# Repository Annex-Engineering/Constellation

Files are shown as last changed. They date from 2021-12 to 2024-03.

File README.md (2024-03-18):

# Constellation
Constellation is a series of control boards, powered by the Raspberry Pi Pico board, developed by the team at ANNEX Engineering.

It is intentional that there are no gerbers/schematics/source files available for the forseeable future. This is to prevent clones popping up that use lower quality components.

## Klipper Configurations

Configurations can be found here

## Supernova
 - Supernova, is a 4 stepper controller. 
 - Can drive steppers at 12v to 48v
 - Supports sensorless or switch based endstops
 - Standard Stepstick format supported only
 - Uses XH or Microfit connectors to connect to steppers, such that currents of 3A+ can be supported

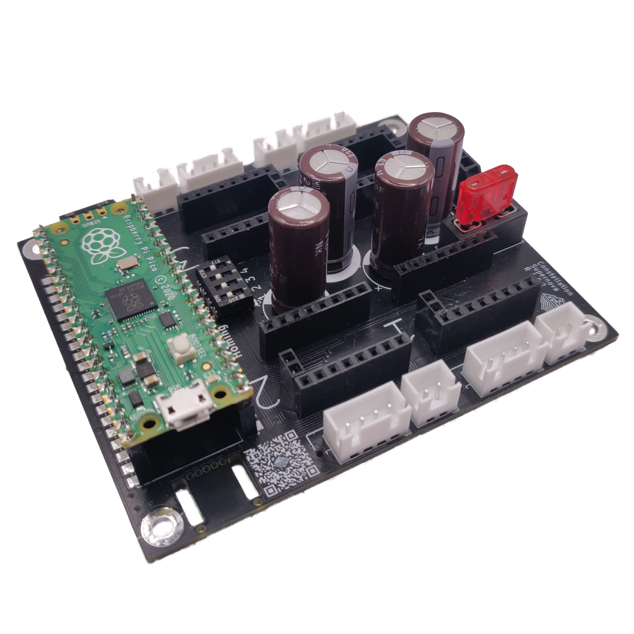
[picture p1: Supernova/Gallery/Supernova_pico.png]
 

 ## Sirius
 TBD

 ## Nebula
 TBD

Our discord server can be found here: 

Join me on Discord (https://discord.gg/MzTR3zE)

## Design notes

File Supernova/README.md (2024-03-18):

# Supernova R1.0.2 - FAQ


Assembled Constellation Supernova R1 with socketed Raspberry Pico.

## Warning
Using 48V electronics can cause serious harm on injury, only attempt to install this on your printer if you know what you are doing.

Under no circumstances we can be held responsible for harm or injury to any person or piece of equipment and you waiver all rights to hold us responsible for anything that happens as a result of using this design, or even thinking about the design.

## Klipper Configurations

Configurations can be found here

## Motor Wiring & Current Limitations

Supernova is rated to handle a total of 8.5 A current combined and up to 48v for all motors. However, most setups will not reach this limit.  
The limit for each individual motor is dependent on the motor itself and the stepper driver used.
When utilizing over 2A on a stepper it's highly recommended to use Microfit instead of JST XH for the stepper wiring.

## Stepper drivers
There are multiple HV-options (beyond 24V), the maximum safe voltage depends on the components the manufacturer puts on the board. This table is an overview for the most used driver chips, the maximum current they can handle (with sufficient cooling) and if they use SPI or UART.  
The following tables are for the step sticks of different manufacturers and which voltage is the maximum safe voltage recommended.  
The tables are using data which has been shamelessly copied from the fine folks at the [powerBrrr-github](https://github.com/tehmaze/PowerBRRR#stepper-drivers). All currents are specified as RMS.

| Driver chip | Max theoretical voltage | Max current | 'SPI' Dipswitch | 
|-|-|-|-|
| TMC2208 |  33V | 2A | Off for UART |
| TMC2209 |  25V | 2.8A | Off for UART |
| TMC2130 |  46V | 1.2A | On for SPI |
| TMC5160 |  **48V** | 3A | On for SPI |

#### BigTreeTech

| Product | Driver chip | Max safe voltage
|-|-|-|
| BigTreeTech TMC2130 | TMC2130 |  42V | 
| BigTreeTech TMC5160 | TMC5160 |  32V | 
| BigTreeTech TMC5160 Pro | TMC5160 |  **48V** | 
| BigTreeTech TMC2208 | TMC2208 |  33V | 
| BigTreeTech TMC2209 | TMC2209 |  25V | 

#### Fysetc
| Product | Driver chip | Max safe voltage
|-|-|-|
| Fysetc TMC2130 | TMC2130 | 42V |
| Fysetc TMC5160| TMC5160 | 32V | 
| Fysetc TMC5160 HV | TMC5160 | **48V** | 
| Fysetc TMC5160 QHV | TMC5160 | **48V** | 
| Fysetc TMC2208 | TMC2208 |  33V | 
| Fysetc TMC2209 | TMC2209 |  25V | 

#### Watterott
| Product | Driver chip | Max safe voltage
|-|-|-|
| Watterott TMC2130 | TMC2130 | 42V | 
| Watterott TMC5160 HV | TMC5160 | **48V** | 
| Watterott TMC2208 | TMC2208 | 33V |
| Watterott TMC2209 | TMC2209 | 25V | 

#### Other
| Product | Driver chip | Max safe voltage
|-|-|-|
| IdeaFormer TMC2130 V1.2 | TMC2130 | 42V |
| Mellow Fly TMC2209 | TMC2209 | 25V |
| Mellow Fly TMC5160 HV | TMC5160 | 42V |
| Mellow Fly TMC5160 HV Pro | TMC5160 | 42V |

## Sensorless Homing
To enable sensorless homing for e.g. Stepper 1 switch the Dipswitch labeled 'Homing' to **On* where '1' is written on the PCB  
Please note, that in the klipper-config most step sticks require diag0 to be set. However the following step sticks are known to require diag1 to be set (instead of diag0)
- Mellow TMC5160 HV
- Watterott TMC5160
- BigTreeTech TMC5160
- BigTreeTech TMC5160 Pro
  
## Dimensions
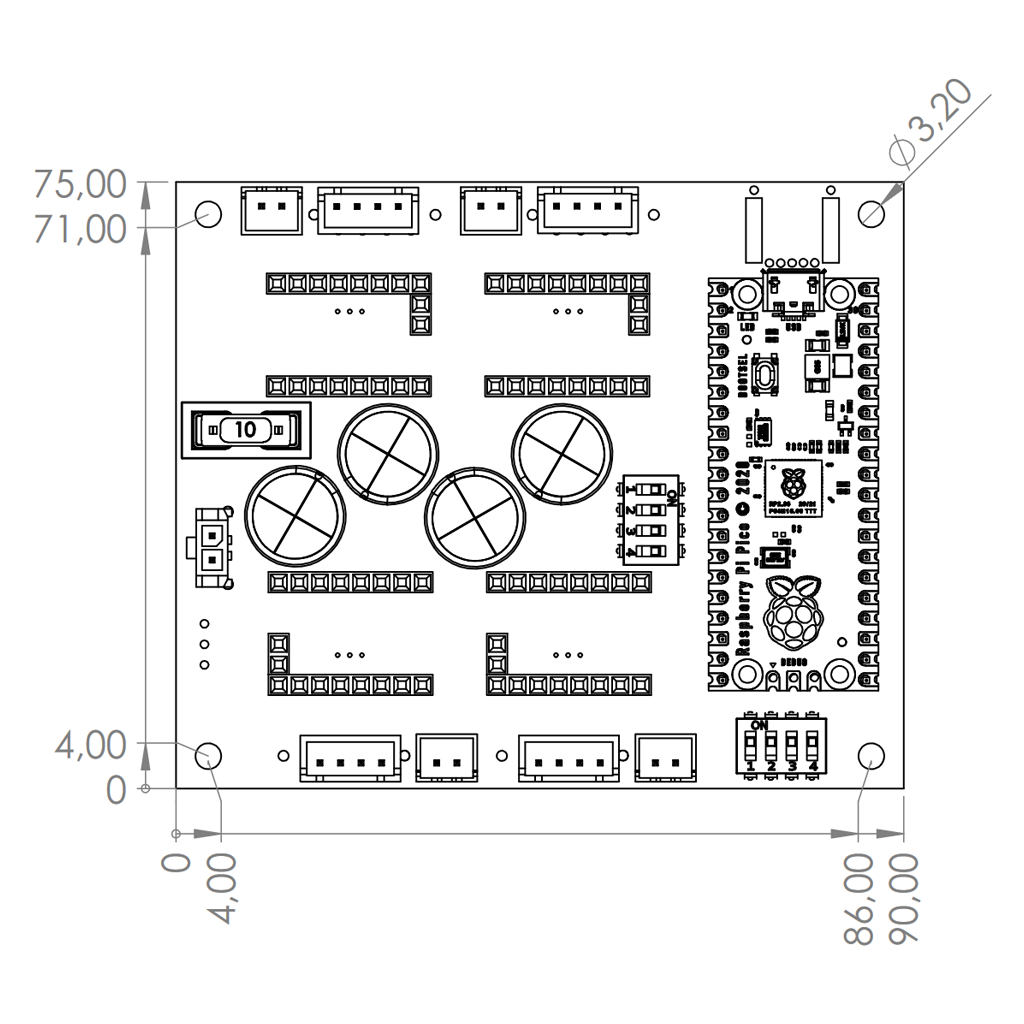
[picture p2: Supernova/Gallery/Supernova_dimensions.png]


The board measures 90x75mm. The mounting holes are spaced apart 82/67mm. 

## Pinout
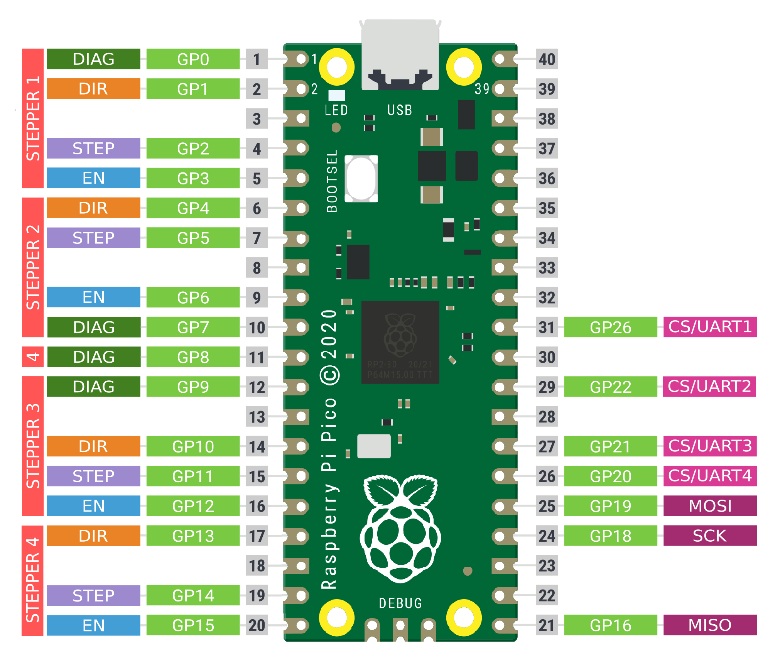
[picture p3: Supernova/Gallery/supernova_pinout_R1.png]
Supernova Pinout


## Flashing Klipper to the Raspberry Pico

> :warning: **If you are using a Raspberry Pi model 4 for Klipper**: Get a good quality USB hub to connect the constellation hardware. The Pi model 4 has a mediocre USB chip that can cause issues in this setup.

To compile the micro-controller code, start by running these commands
on the Raspberry Pi:

```
cd ~/klipper/
make menuconfig
```

Select the Raspberry Pico as controller and review any other options provided. One can enable in the menu to turn on a green LED indicator when powered on. Once configured, run:

```
make
```

Once compiled transfer the .UF2 file to the storage of the Raspberry Pico. This can be done by holding down the button and connecting it to the computer. It will show up as storage device in your file explorer. When done copying to the device it will automatically unmount. The Raspberry Pico is now flashed and ready for use.

Enabling a green LED when powered on can also be done afterwards in the printer.cfg by adding the following:

```
[output_pin power_LED]
pin: gpio25
value: 1
```

## Gallery
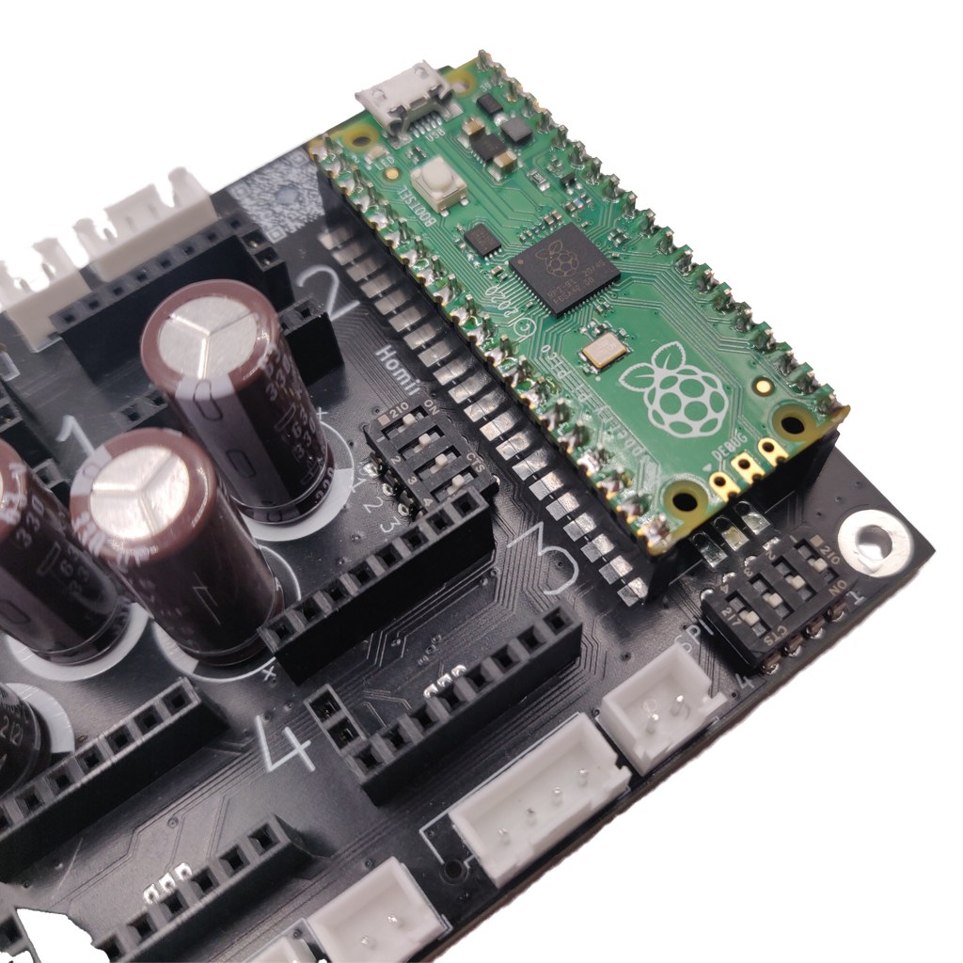
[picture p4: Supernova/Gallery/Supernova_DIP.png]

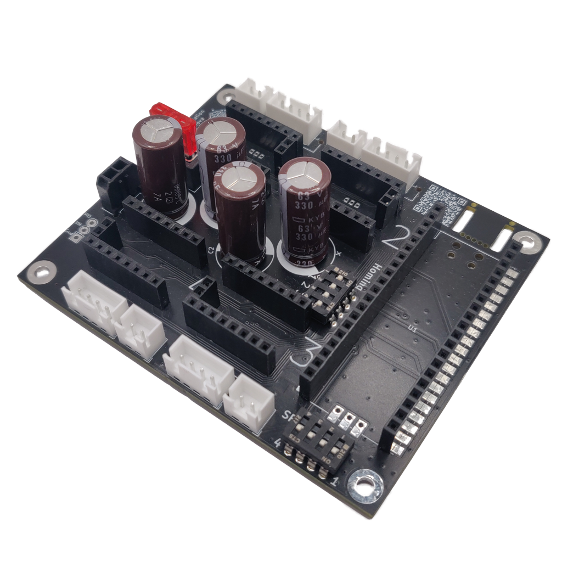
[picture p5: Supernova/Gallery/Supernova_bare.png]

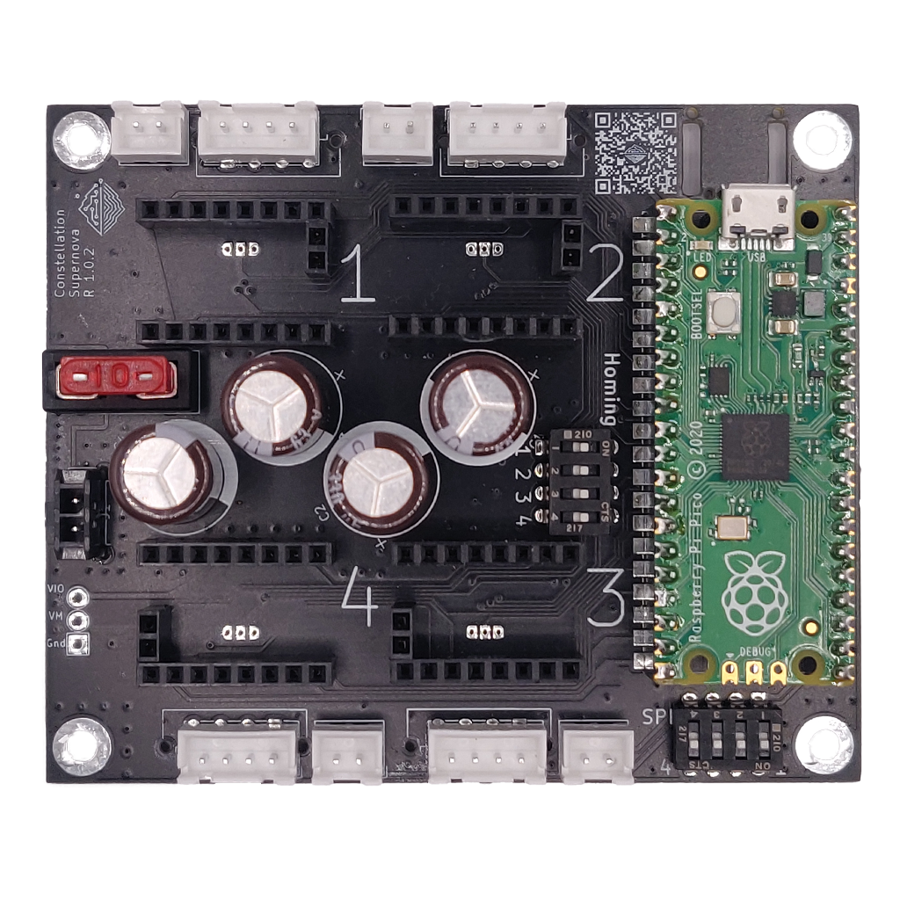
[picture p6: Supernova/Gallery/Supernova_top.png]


## Sourcing
Links to purchase fully assembled boards can be found here: [ANNEX Sourcing Guide](https://docs.google.com/spreadsheets/d/1aSM1jGxg-s0tyynyR3f8M0IQMXuXw57RJvoJbt98Clw/edit?usp=sharing)

Our discord server can be found here: 

Join me on Discord (https://discord.gg/MzTR3zE)

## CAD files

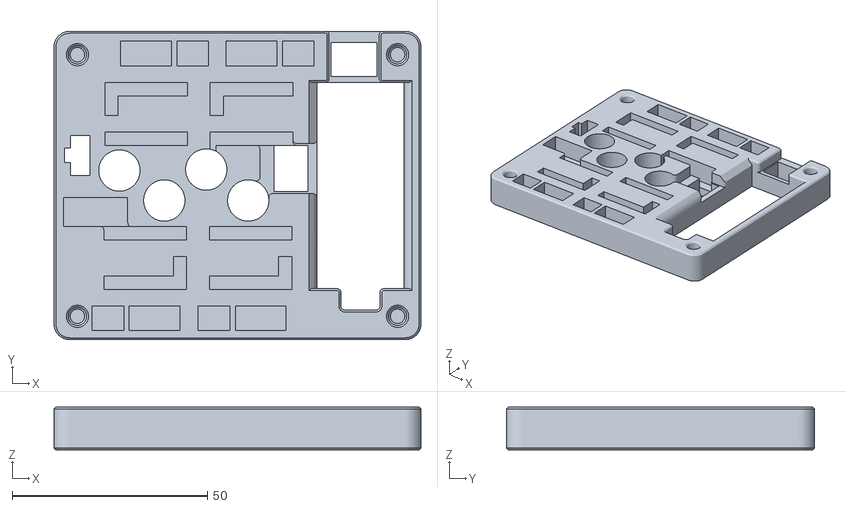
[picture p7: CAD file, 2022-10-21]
Supernova/Assembly_Jig/supernova_assembly_jig_10-21-22_10mm_caps.stl
94.0 x 79.0 x 11.0

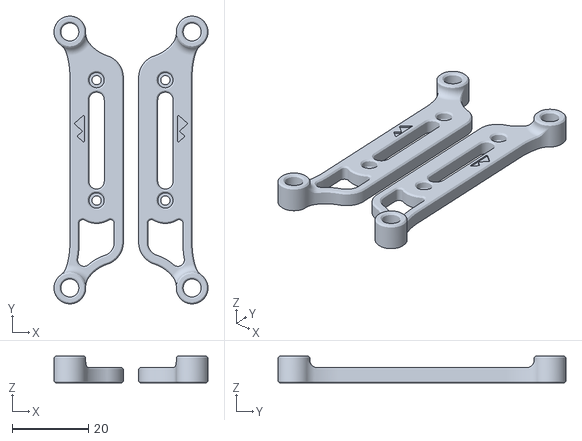
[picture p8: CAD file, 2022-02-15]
Supernova/STLs/single_constellation_bracket_voron_din_x1_rev1.STL
40.3 x 75.3 x 7.00

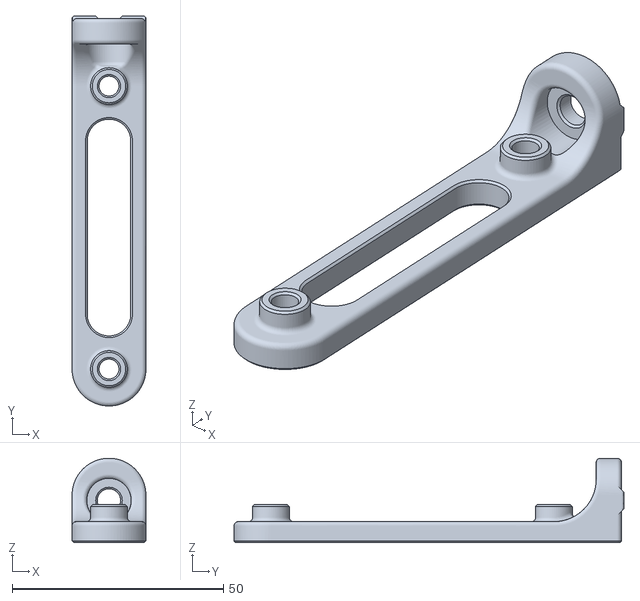
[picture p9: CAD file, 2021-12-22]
Supernova/STLs/single_constellation_bracket_x2_rev1.STL
17.5 x 92.4 x 20.0

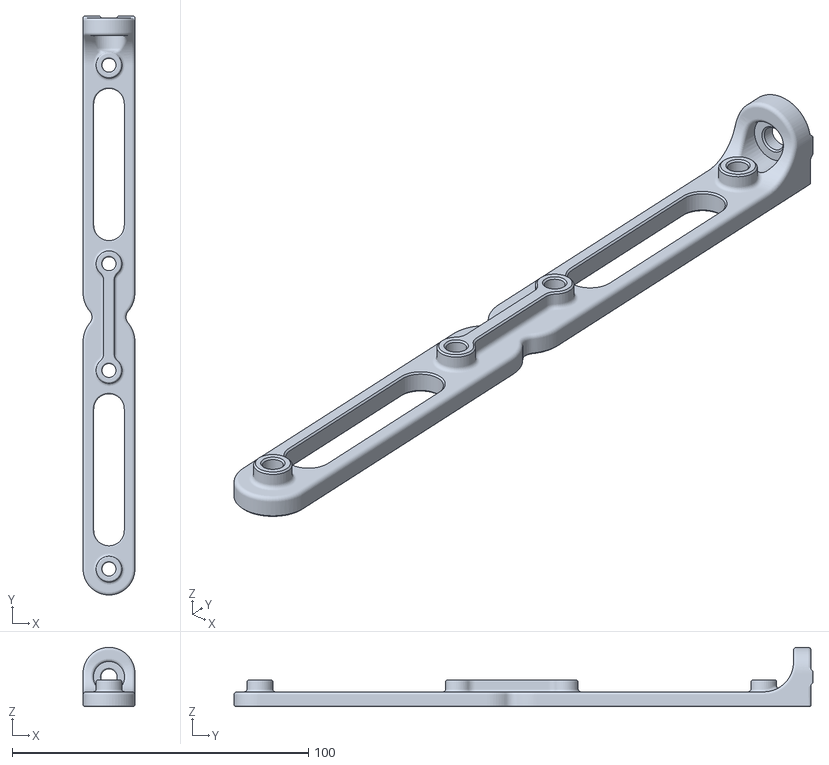
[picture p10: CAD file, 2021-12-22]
Supernova/STLs/dual_constellation_bracket_x2_rev1.STL
17.5 x 195.3 x 20.0

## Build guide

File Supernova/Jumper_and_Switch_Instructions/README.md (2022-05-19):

# Supernova - Jumper and Switch Instructions

## Sensorless Homing
 - flip the Dip-switch to 'On' (numbers under each dip for the number of driver)
 - flip to off to use the endstop header

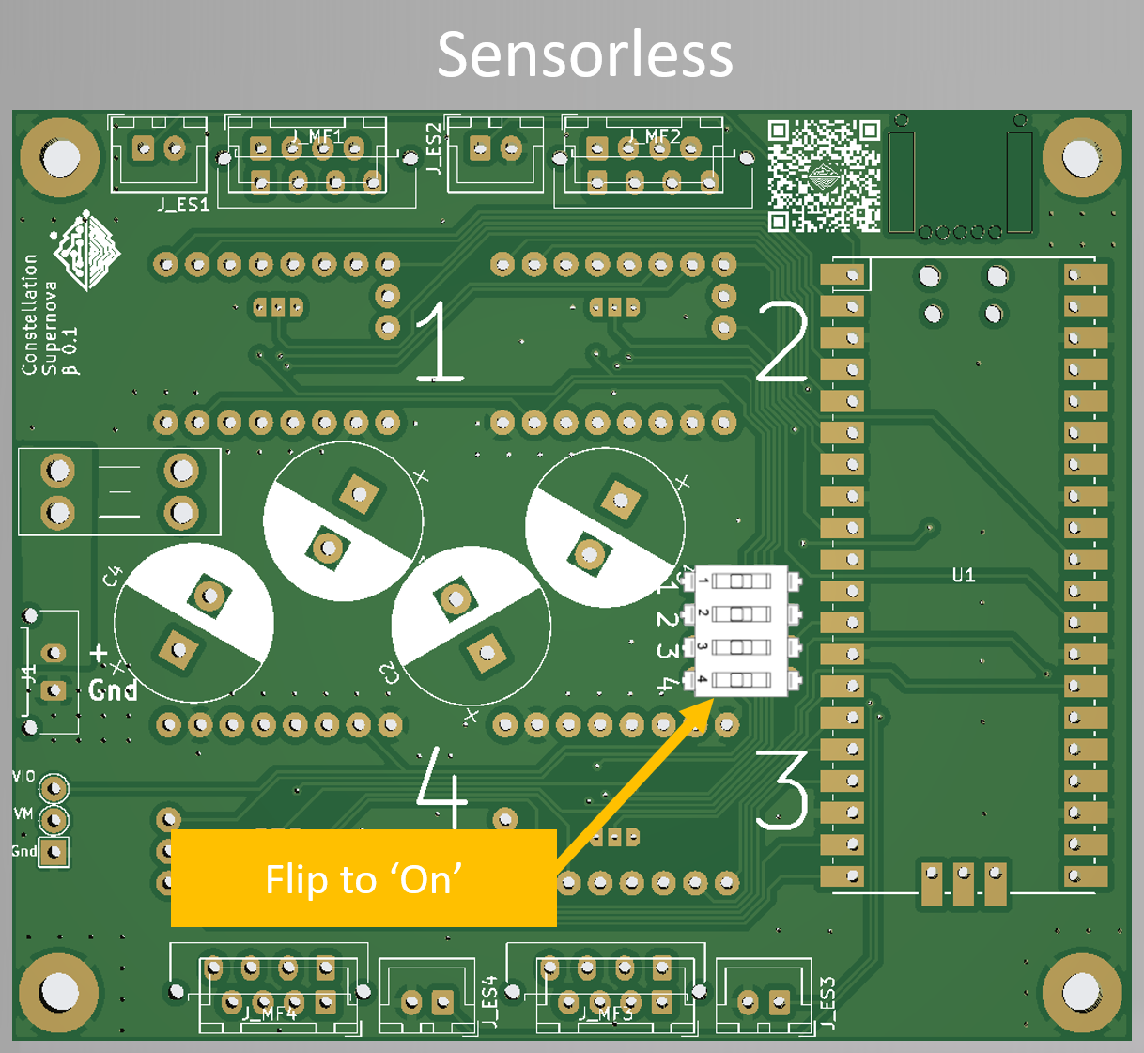
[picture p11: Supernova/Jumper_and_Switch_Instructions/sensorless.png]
Image of Sensorless Cluster

 
## SPI Jumpers
 - flip the Dip-Switch to 'On' to use SPI (starting with driver 4 from the left going to number 1 at the right)
 - flip to 'Off' to use UART
 
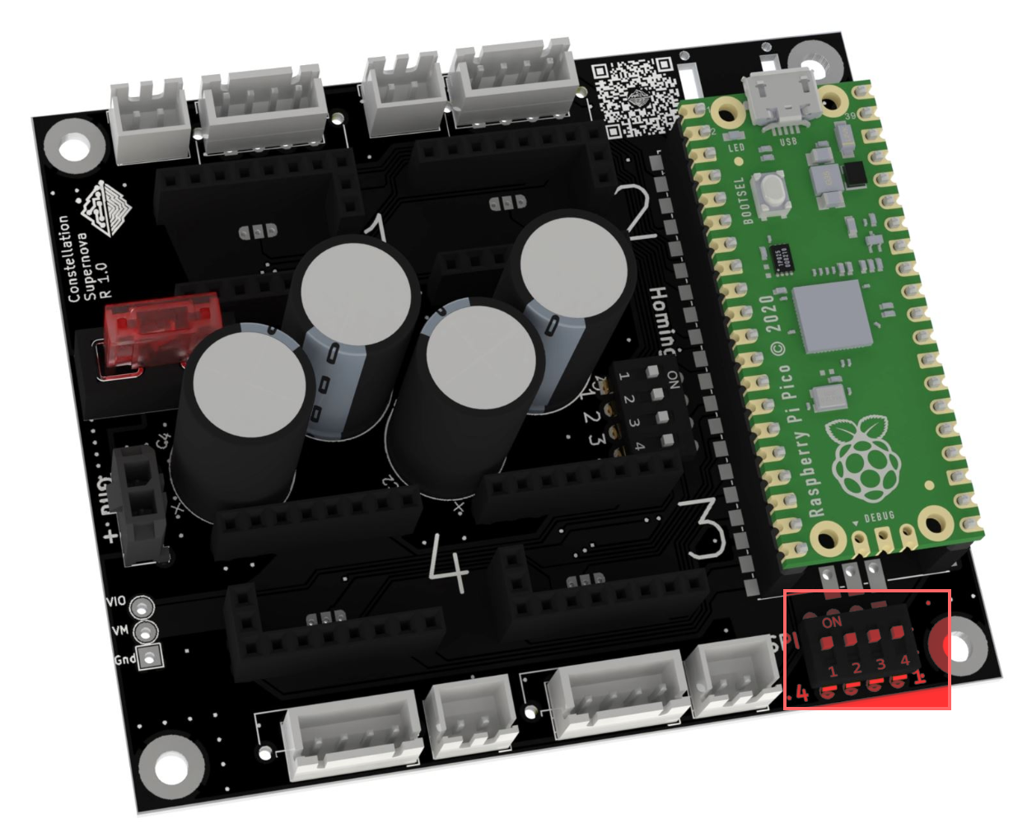
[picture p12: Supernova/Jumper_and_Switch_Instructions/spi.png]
Image of SPI Jumpers


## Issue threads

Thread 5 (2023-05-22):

Schematic and Endstop Pin Voltage

brotherdust, 2023-05-22:
Hi!
This is a nice and simple board and I've had good luck with it. I wanted to try to make it so I can use a SuperPINDA as the endstop for my z-axis, so I flipped the related DIP switch and checked the voltage and polarity on the pins. It looks like the endstop pins only output 2.5v, which is lower than what I can power my PINDA with. I figure I can power it from elsewhere, so no big deal there. The question is how these endstop pins are wired. Since there's no schematic, I can't see where the power for the pins comes from nor the MCU pin it should be connected to. Presumably, the input pin is the same that was connected to the DIAG pin previously for sensorless homing.

Anyway, long story short, can you please provide schematics for this board? It would be very helpful.
Thanks!

Kirinkunhime, 2023-05-22:
Hi !

I think you might have gotten a few things mixed up. The Dip switch does not need to be turned on when using an endstop - in your case you might have connected the Diag-pins of the Driver with the endstop (which is not how it's supposed to be used)

The Endstop pins go straight towards the DIAG1/2/3/4 pins on the Pico respectively.
The other pin is connected directly to ground.

As for the schematics, I've mentioned it quite often when poked in Discord but Supernova (as well as future constellation boards) will be fully closed source. This includes me not even sharing schematics.
While I personally don't like having to take this step, I kindly ask for your understanding, but that goes onto a bit of a longer rant. But basically, inside the DIY 3D printing community the somewhat recent culture has become to take something someone else made, slap spin it up slightly differently and call it your own thing.
While there have been notable exceptions (shoutout to the peeps from the CroXY discord that e.g. credited the Carabiner as inspirations/similar designs), more often than not things will just be copied and if similarties are pointed out they're just ignored.

So once again I apologize for not providing schematics, but hope that I could help you with your issue regarding the SuperPINDA.

Also, after looking into the SuperPinda wiring really quick I'd not recommend using the SuperPinda with Supernova - this is due to the SuperPinda likely pulling up the sensor pin to 5V when it detects it's close enough. However, the Pico does not handle 5V on it's pins - it's limited to 3.3V.
But, with multi MCU homing it should be possible to connect the SuperPinda on another board (that you're likely running anyways for your heaters, as Supernova does not support it)

brotherdust, 2023-05-22:
I appreciate your candor and completely understand your position. Sorry I missed the Discord thing; I am strongly against using Discord and its ilk as a "source of truth"/documentation for _any_ project, to tend to avoid using it. May I recommend that you update your _documentation_ here on the repo to reflect your position? As a courtesy and a benefit to the community, I'll gladly author a PR if you lack the time. Thanks much!

Closed 2023-05-22.

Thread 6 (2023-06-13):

Did not hold dimensioning while printing/pi died

Mubbler, 2023-06-13:
Two 5160 pro at 48v 2.8a running nema 23.

When jogging the dimensioning held up nicely but while printing the dimensioning started to fail (ie needed 45mm but when 43mm). Eventually one of  the motors started  to visibly stall for brief periods of times  during homing and some prints. The pi that came with the unit died shortly after this. Thinking the pi was the issue wondering or if I was pushing the board to hard.

Trails5000, 2023-06-13:
you didnt mention what drivers you are using, the drivers are probably overheating

Mubbler, 2023-06-13:
The btt 5160pros
https://www.amazon.com/gp/product/B0B8HZXWPP/ref=ppx_yo_dt_b_search_asin_title?ie=UTF8&psc=1
They were not hot to the touch, and the pi no longer would show up in the device list when I checked for it.

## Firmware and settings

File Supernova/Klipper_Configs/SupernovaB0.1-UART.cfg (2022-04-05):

# Supernova A0.2 - UART mode (specific for BTT TMC2209 V1.2)
# Check github for more information about how to setup the jumpers and pads

##########################################
# 	 General settings
##########################################

[mcu]
serial:


##########################################
# 	 Stepstick slots
##########################################


[stepper_x]					#Stepper 1 on the PCB
step_pin: gpio2
dir_pin: gpio3
enable_pin: !gpio1
endstop_pin: gpio0
position_endstop: 250
position_max: 250
homing_speed: 40
microsteps: 16
rotation_distance: 40
full_steps_per_rotation: 400

[stepper_y]					#Stepper 2 on the PCB
step_pin: gpio7
dir_pin: gpio6
enable_pin: !gpio5
endstop_pin: gpio4
position_endstop: 250
position_max: 250
homing_speed: 40
microsteps: 16
rotation_distance: 40
full_steps_per_rotation: 400

[stepper_z]					#Stepper 3 on the PCB
step_pin: gpio11
dir_pin: gpio10
enable_pin: !gpio8
endstop_pin: gpio9
position_endstop: 250
position_max: 250
homing_speed: 40
microsteps: 16
rotation_distance: 40
full_steps_per_rotation: 400

[stepper_z1]				#Stepper 4 on the PCB
step_pin: gpio13
dir_pin: gpio14
enable_pin: !gpio12
endstop_pin: gpio15
position_endstop: 250
position_max: 250
homing_speed: 40
microsteps: 16
rotation_distance: 40
full_steps_per_rotation: 400


##########################################
# 	 Driver settings
##########################################

[tmc2209 stepper_x]
uart_pin: gpio26
interpolate: True
run_current: 0.8
hold_current: 0.8
stealthchop_threshold: 0	#It is recommended to keep stealthchop disabled
#diag: gpio0

[tmc2209 stepper_y]
uart_pin: gpio22
interpolate: True
run_current: 0.8
hold_current: 0.8
stealthchop_threshold: 0
#diag: gpio4

[tmc2209 stepper_z]
uart_pin: gpio21
interpolate: True
run_current: 0.8
hold_current: 0.8
stealthchop_threshold: 0
#diag: gpio9

[tmc2209 stepper_z1]
uart_pin: gpio20
interpolate: True
run_current: 0.8
hold_current: 0.8
stealthchop_threshold: 0
#diag: gpio15

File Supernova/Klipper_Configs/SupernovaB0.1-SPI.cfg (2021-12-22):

# Supernova B0.1 - SPI Mode
# Check github for more information about how to setup the jumpers and pads

##########################################
# 	 General settings
##########################################

[mcu]
serial:


##########################################
# 	 Stepstick slots
##########################################


[stepper_x]					#Stepper 1 on the PCB
step_pin: gpio2
dir_pin: gpio1
enable_pin: !gpio3
endstop_pin: gpio0
position_endstop: 250
position_max: 250
homing_speed: 40
microsteps: 16
rotation_distance: 40
full_steps_per_rotation: 400

[stepper_y]					#Stepper 2 on the PCB
step_pin: gpio5
dir_pin: gpio4
enable_pin: !gpio6
endstop_pin: gpio7
position_endstop: 250
position_max: 250
homing_speed: 40
microsteps: 16
rotation_distance: 40
full_steps_per_rotation: 400

[stepper_z]					#Stepper 3 on the PCB
step_pin: gpio11
dir_pin: gpio10
enable_pin: !gpio12
endstop_pin: gpio9
position_endstop: 250
position_max: 250
homing_speed: 40
microsteps: 16
rotation_distance: 40
full_steps_per_rotation: 400

[stepper_z1]				#Stepper 4 on the PCB
step_pin: gpio14
dir_pin: gpio13
enable_pin: !gpio15
endstop_pin: gpio8
position_endstop: 250
position_max: 250
homing_speed: 40
microsteps: 16
rotation_distance: 40
full_steps_per_rotation: 400


##########################################
# 	 Driver settings
##########################################

[tmc5160 stepper_x]
sense_resistor: 0.075		#BTT en Mellow use 0.075 instead of the stock 0.110 value
cs_pin: p:gpio26
spi_bus: spi0c
run_current: 0.8
hold_current: 0.8
stealthchop_threshold: 0	#It is recommended to keep stealthchop disabled

[tmc5160 stepper_y]
sense_resistor: 0.075
cs_pin: p:gpio22
spi_bus: spi0c
run_current: 0.8
hold_current: 0.8
stealthchop_threshold: 0

[tmc5160 stepper_z]
sense_resistor: 0.075
cs_pin: p:gpio21
spi_bus: spi0c
run_current: 0.8
hold_current: 0.8
stealthchop_threshold: 0

[tmc5160 stepper_z1]
sense_resistor: 0.075
cs_pin: p:gpio20
spi_bus: spi0c
run_current: 0.8
hold_current: 0.8
stealthchop_threshold: 0

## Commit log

2021-12-22 create repo
    [dual_constellation_bracket_x2_rev1.STL, single_constellation_bracket_x2_rev1.STL]
2021-12-22 add klipper configs
    [SupernovaB0.1-SPI.cfg, Supernova_A0.2_-_SPI_mode.cfg, Supernova_A0.2_-_UART_mode.cfg]
2021-12-23 add sensorless photo
2021-12-30 Create SupernovaB0.1-SPI - Trails_Sensorless_5160HV_example.cfg
    [SupernovaB0.1-SPI - Trails_Sensorless_5160HV_example.cfg]
2022-01-03 Create SupernovaB0.1-SPI - CartesianXY_Sensorless_5160HV_example.cfg
    [SupernovaB0.1-SPI - CartesianXY_Sensorless_5160HV_example.cfg]
2022-01-09 Generalize SPI beta config Add UART beta config Move Alpha configurations in a dedicated subfolder
    [SupernovaB0.1-UART.cfg, Supernova_A0.2_-_SPI_mode.cfg, Supernova_A0.2_-_UART_mode.cfg]
2022-02-15 add voron din bracket for single constellation board by request
    ugh
    [single_constellation_bracket_voron_din_x1_rev1.STL]
2022-03-21 Update SupernovaB0.1-UART.cfg
    Add optional diag pin
    [SupernovaB0.1-UART.cfg]
2022-04-17 Supernova R1
    [Supernova-R1-SPI - CartesianXY_Sensorless_5160HV_example.cfg, Supernova-R1-SPI - Trails_Sensorless_5160HV_example.cfg, Supernova-R1-SPI.cfg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]
2022-05-12 Update README.md
    Added the Fysetc 5160 QHV and Mellow Fly HV TMC5160 Pro drivers. The Mellow/Fly drivers should be adjusted to 42V max recommendations as the capacitors that they use are rated 50V, it is not safe to 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
2022-05-16 Publish R1 simplified CAD.
    This should allow people to build enclosures with the Supernova.
    [Supernova_R1_CAD_simplified.STEP]
2022-05-19 Update SPI instructions
2022-05-31 Update Supernova-R1-UART.cfg
    Fix incorrect pins
    [Supernova-R1-UART.cfg]
2022-06-02 Replace with more detailed CAD
    [Supernova_R1_CAD_simplified.STEP]
2022-10-21 Update supernova_assembly_jig_10-21-22_10mm_caps.stl
    more switch clearance
    [supernova_assembly_jig_10-21-22_10mm_caps.stl]
2023-02-15 Update README.md
    Derate max current to 8.5 A - it should handle more but better be safe than sorry
2023-11-27 clean house for configs repo
    [Supernova-R1-SPI - CartesianXY_Sensorless_5160HV_example.cfg, Supernova-R1-SPI - Trails_Sensorless_5160HV_example.cfg, Supernova-R1-SPI.cfg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]
